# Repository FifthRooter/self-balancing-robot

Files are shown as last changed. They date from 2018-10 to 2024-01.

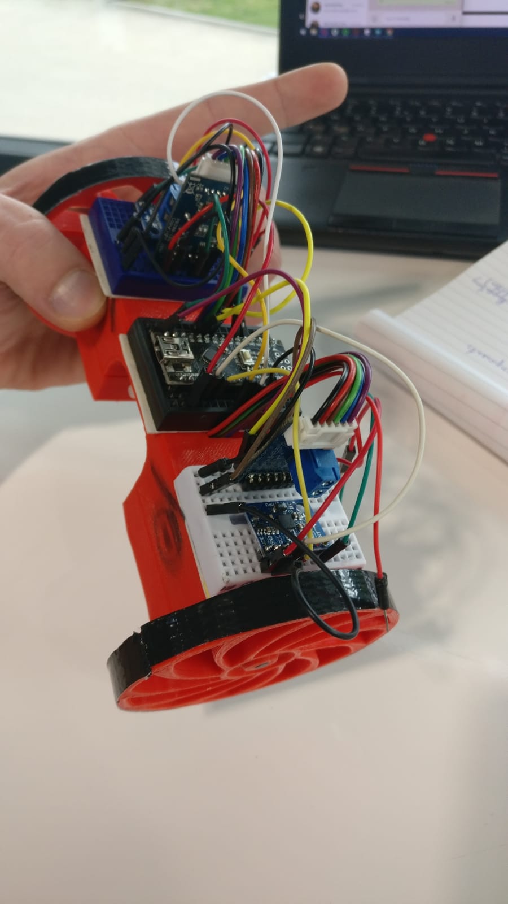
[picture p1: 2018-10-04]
graphics/v1/mark-1-angle.jpeg

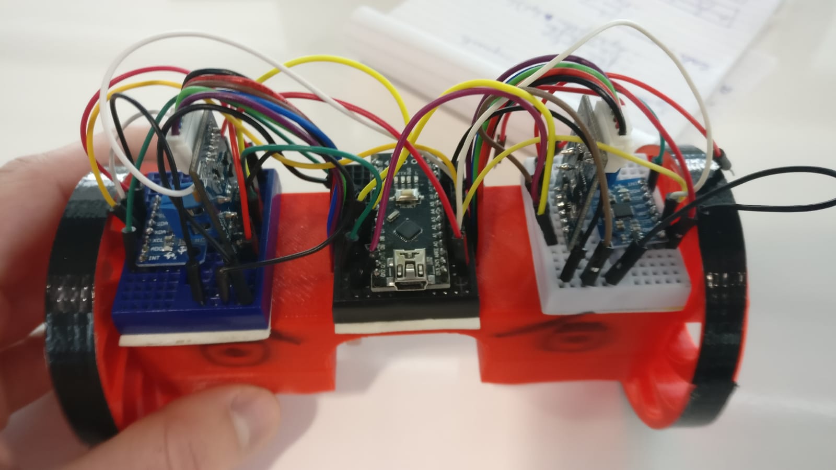
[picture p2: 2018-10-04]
graphics/v1/mark-1-top.jpeg

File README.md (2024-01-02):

### Self-balancing robot

https://github.com/FifthRooter/self-balancing-robot/assets/22204845/546c1cc7-7c90-414c-b639-572d04be5377

#### Overview
The robot is equipped with two MPU-6050 sensors that contain a 3-axis MEMS accelerometer and a 3-axis MEMS gyroscope.
The two sensors are placed at each end of the robot (above the wheels) for greater accuracy.

The design files (STLs and Solidworks) can be found in the repo under /design.

Both the accelerometer and the gyroscope individually are not sufficient to provide quality data that can be used to correct the robot’s tilt and always keep it aligned. 

That’s because the gyroscope only measures angular velocity which means that there is no fixed reference point apart from the initial calibration that can be done at the beginning of the robot test by aligning it properly and using the velocity measurements to calculate angular displacement and correct the robot accordingly. 

This requires integrating the velocity data, which would quickly become useless as integration would increase the error with time, rendering the original reference point moot. Every angular displacement calculation would contain an error, which would keep adding up with every integration step, leading to an increasingly larger errors, making the system unstable.

The accelerometer, however, can be used without the gyroscope, as the angular displacement and velocity can be calculated by performing a double and single integration, respectively. The issue is that it cannot measure precise enough acceleration values for the project’s purposes. As the accelerometer measures acceleration, it also measures the gravitational pull of Earth, which output value would be read as 1g. This 1g reference point can be used to determine orientation relative to ground.

Thus, the accelerometer and gyroscope are an ideal combination (sensor fusion) to measure the orientation and the angular velocity of the robot, allowing for accurate compensation calculations that could be used to actuate the motors in order to keep the robot stable. A complementary filter has been implemented to merge the accelerometer and gyroscope data for greater accuracy:
complementary-filter

The robot uses a proportional-integral-derivative controller (PID) to ensure that it’s always balanced with its z-axis aligned with the gravitational pull of the planet:


Electrical diagram of the whole system:
self-balancing-robot-diagram

Electrical components:
- 2x 1:53 6V DC motors
- 2x H-bridges for motor control
- Arduino Nano
- Optional: ESP8266 for wireless control
- Optional: RPi + camera for vision
- 2x MPU-6050 sensors
- Boost converter
- 2x 18650 3.7V batteries

Libraries used:
- Wire.h  - enables communication with I2C devices (small serial devices)
- I2Cdev.h - enables interfacing/reading data from a I2C device
- MPU6050.h - allows for reading data from the MPU-6050 board

Electrical components:
- 2x 1:53 6V DC motors
- 2x H-bridges for motor control
- Arduino Nano
- Optional: ESP8266 for wireless control
- Optional: RPi + camera for vision
- 2x MPU-6050 sensors
- Boost converter
- 2x 18650 3.7V batteries

Libraries used:
- Wire.h  - enables communication with I2C devices (small serial devices)
- I2Cdev.h - enables interfacing/reading data from a I2C device
- MPU6050.h - allows for reading data from the MPU-6050 board

mark-1-angle
mark-1-front
mark-1-side
mark-1-top
mark-bottom

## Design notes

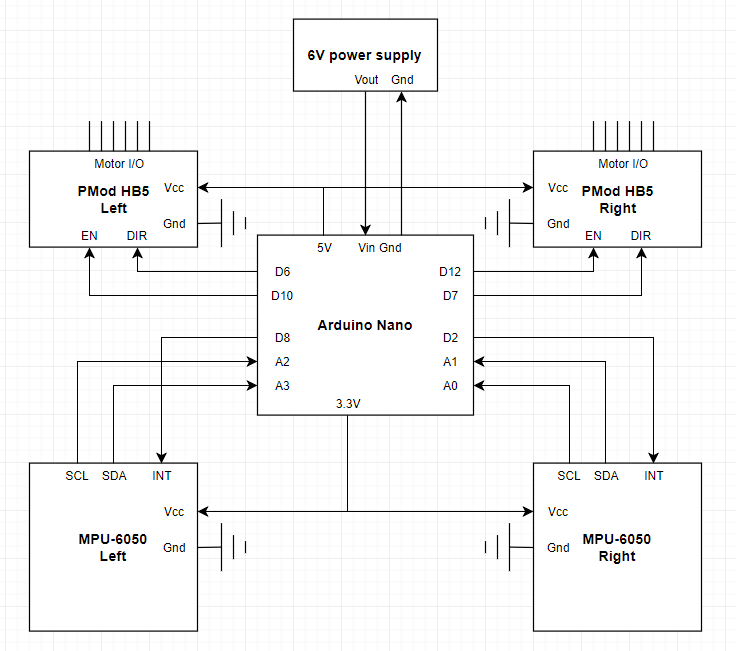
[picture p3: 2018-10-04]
graphics/diagrams/self-balancing-robot-diagram.png

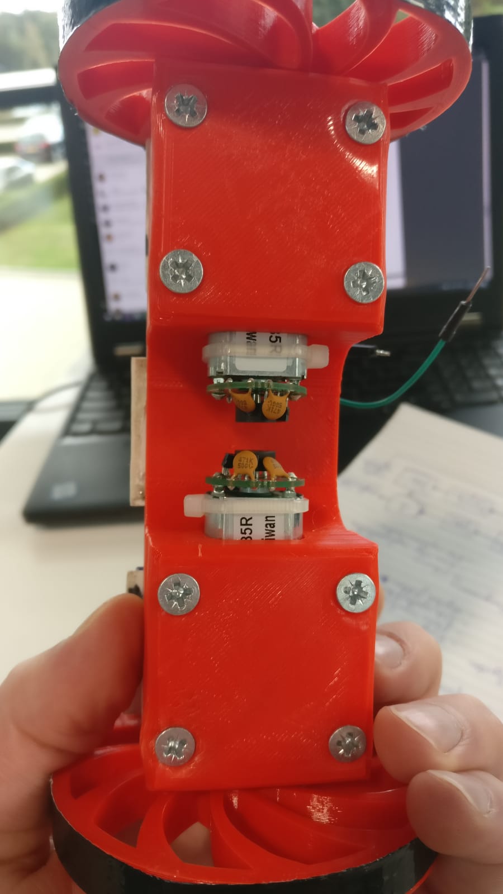
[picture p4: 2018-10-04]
graphics/v1/mark-bottom.jpeg

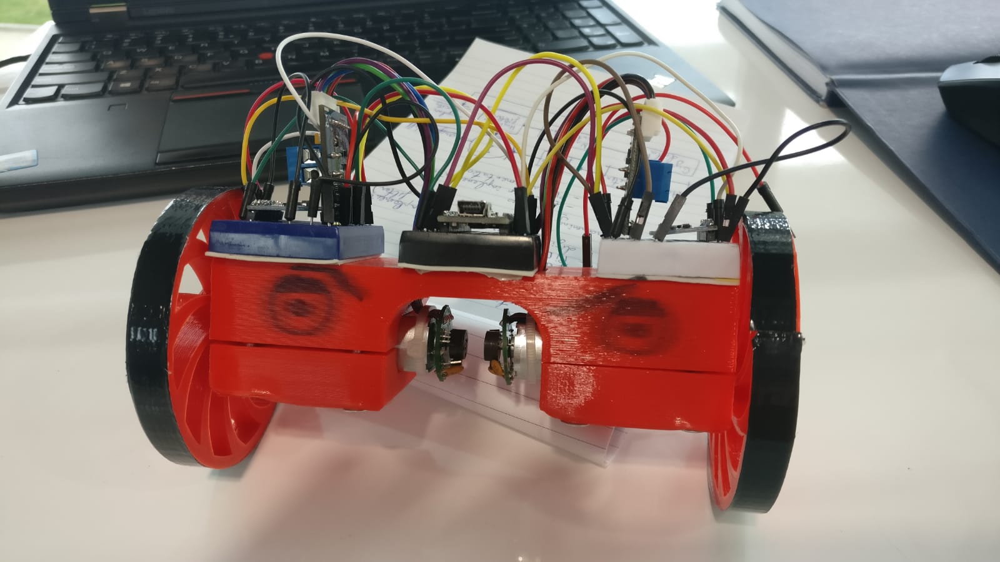
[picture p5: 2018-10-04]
graphics/v1/mark-1-front.jpeg

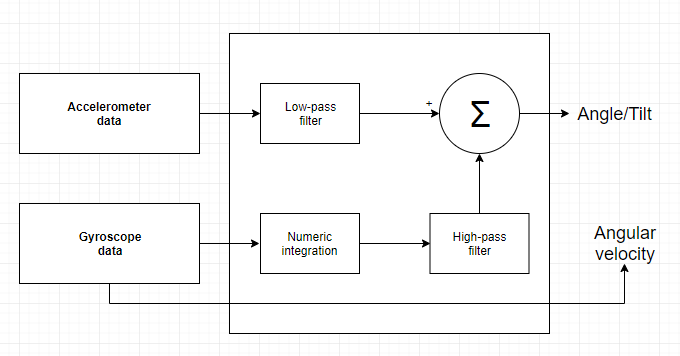
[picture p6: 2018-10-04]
graphics/diagrams/complementary-filter.png

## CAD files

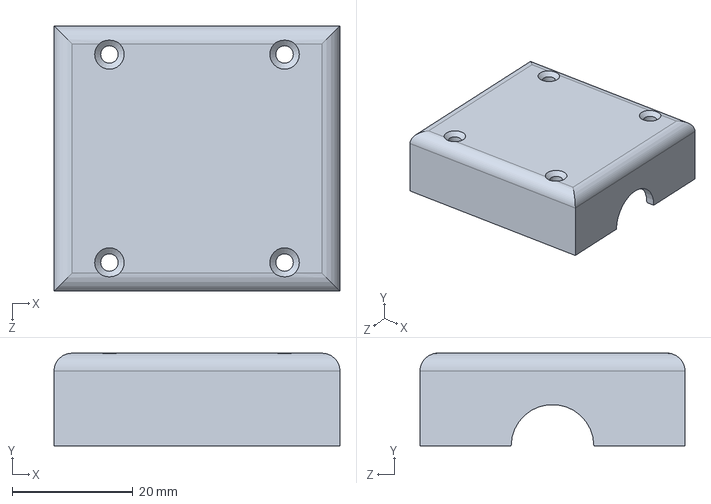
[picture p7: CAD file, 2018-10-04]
3d-design/v1/motor_sandwich.SLDPRT
47.5 x 15.4 x 44.0 mm

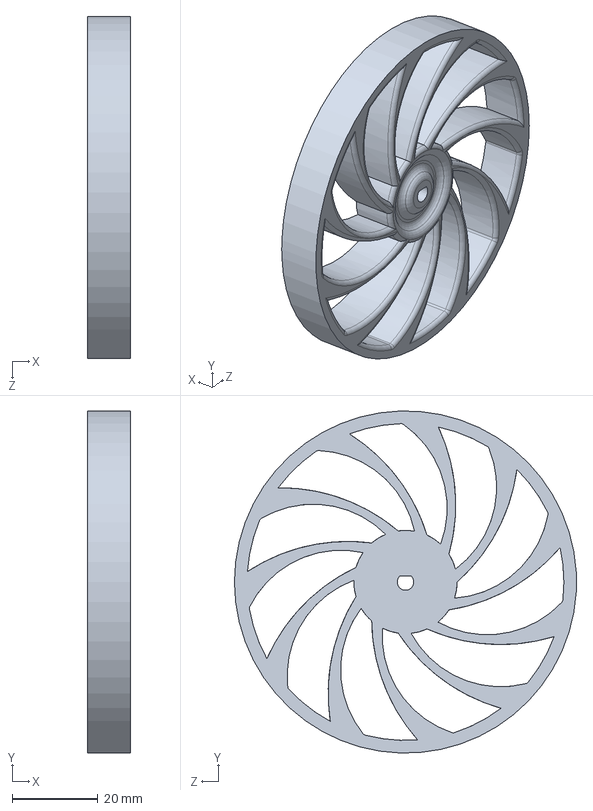
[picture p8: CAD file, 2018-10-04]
3d-design/v1/wheel.SLDPRT
10.0 x 80.0 x 80.0 mm

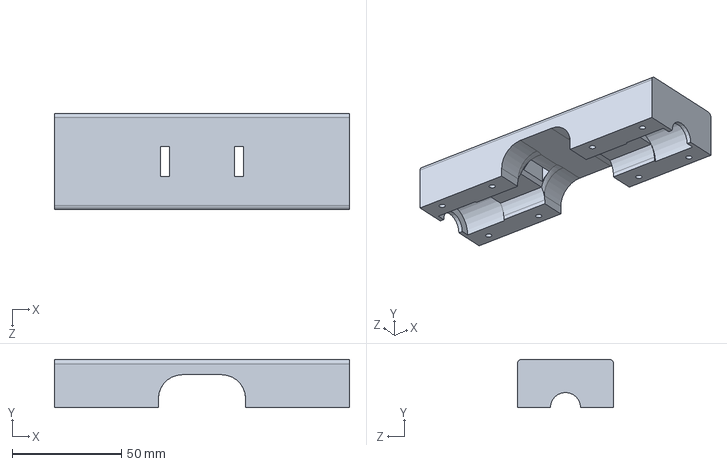
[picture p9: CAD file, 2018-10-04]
3d-design/v1/platform.SLDPRT
134.7 x 22.0 x 44.0 mm

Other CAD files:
3d-design/v1/motor_sandwich.STL
3d-design/v1/platform.STL
3d-design/v1/wheel.STL

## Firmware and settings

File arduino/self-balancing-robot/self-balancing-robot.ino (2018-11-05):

#include "Wire.h"
#include "I2Cdev.h"
#include "MPU6050.h"
#include "math.h"


MPU6050 mpu;                                    // Create an instance of the MPU6050 class

int16_t accY, accZ;                             // Define accelerometer Y and Z values as 16bit integers
float accAngle;                                 // Define the angle that will be calculated using accY and accZ values

int16_t gyroX;                                  // Define gyroscope X value (angular velocity around x-axis) as 16bit integer
float gyroAngle = 0;                            // Give the gyro angle an initial value of 0
unsigned long currTime, prevTime = 0, loopTime; // Set time-related variables as 32bit numbers of only positive value (0 to 2^32-1)

#define direction_left 5                        // Set pin number for DIR pin of left motor
#define direction_right 8                       // Set pin number for DIR pin of right motor
#define motor_pwm_left 6                        // Set pin number for EN- pin of left motor (must be a PWM pin)
#define motor_pwm_right 11                      // Set pin number for EN pin of right motor (must be a PWM pin)

#define Kp 36 // Set the proportional gain value for the PID controller
#define Ki 16.6667 //33.3333                                  //0.003 // Set the derivative gain value for the PID controller
#define Kd 0.015//0.0075
#define sampleTime 0.005                        // Define sampling time
#define targetAngle 0.5                           // Define target angle which is the desired tilt of the robot

float a = 0.0;
float tau = 0.075;
float x_angle = 0.0;

// Declare variables that are shared between the interrupt function and main loop as volatile to avoid compiler attempt to optimize the shared objects
volatile int motorPower, gyroRate;
volatile float currentAngle, prevAngle = 0, error, prevError = 0, errorSum = 0;

float complementaryFilter(float newAngle, float gyroRate, int loopTime) {
  float dtC = float(loopTime)/1000.0;
  a = tau / (tau+dtC);
  x_angle = a * (x_angle + gyroRate*dtC) + (1-a)*(newAngle);
  return x_angle;
}

void setMotors(int leftMotorSpeed, int rightMotorSpeed) {
  if (leftMotorSpeed <= 0) {
    leftMotorSpeed = leftMotorSpeed * (-1);
    leftMotorSpeed = map(leftMotorSpeed, 0, 255, 22, 255); // CCW
    analogWrite(motor_pwm_left, leftMotorSpeed);
    digitalWrite(direction_left, HIGH);
  } else {
    leftMotorSpeed = map(leftMotorSpeed, 0, 255, 22, 255); // CW
    analogWrite(motor_pwm_left, leftMotorSpeed);
    digitalWrite(direction_left, LOW);
  }

  if (rightMotorSpeed <= 0) {
    rightMotorSpeed = rightMotorSpeed * (-1);
    rightMotorSpeed = map(rightMotorSpeed, 0, 255, 0 , 255); // CW
    analogWrite(motor_pwm_right, rightMotorSpeed);
    digitalWrite(direction_right, LOW);
  } else {
    rightMotorSpeed = map(rightMotorSpeed, 0, 255, 0, 255); //CCW
    analogWrite(motor_pwm_right, rightMotorSpeed);
    digitalWrite(direction_right, HIGH);
  }
}


void initPID() {
  // initialize timer
  cli();
  TCCR1A = 0;
  TCCR1B = 0;

  OCR1A = 19999; // match register = (16000000Hz / (8*desired_frequency)) - 1 ; currently the frequency is 200HZ(5ms)
  TCCR1B |= (1 << WGM12);
  TCCR1B |= (1 << CS11);
  TIMSK1 |= (1 << OCIE1A);

  sei();
}

void setup() {
  mpu.initialize();
  Serial.begin(115200);

  pinMode(direction_left, OUTPUT);
  pinMode(direction_right, OUTPUT);
  pinMode(motor_pwm_left, OUTPUT);
  pinMode(motor_pwm_right, OUTPUT);

  mpu.setYAccelOffset(-205);
  mpu.setZAccelOffset(1398);
  mpu.setXGyroOffset(-45);

  initPID();
}

void loop() {
  // read sensor data
  accY = mpu.getAccelerationY();
  accZ = mpu.getAccelerationZ();
  gyroX = mpu.getRotationX();
  //Serial.println("accY: " + accY);
  //define the range of motor input
  motorPower = constrain(motorPower, -255, 255);
  setMotors(motorPower, motorPower);
}

ISR(TIMER1_COMPA_vect) {
  // calculate angle of inclination
  accAngle = atan2(accY, accZ) * RAD_TO_DEG;
  gyroRate = map(gyroX, -32768, 32768, -250, 250);
  gyroAngle = (float)gyroRate * sampleTime;
  //currentAngle = 0.98 * (prevAngle + gyroAngle) + 0.02 * (accAngle);
  currentAngle = complementaryFilter(accAngle, gyroRate, sampleTime*1000);
  //Serial.print(accY);
  //Serial.print(",");
  //Serial.print(accZ);
  //Serial.print(",");
  //Serial.print(gyroRate);
  //Serial.print(",");

  error = currentAngle - targetAngle;
    errorSum = errorSum + error/2*sampleTime;

  // calculate output from PID values
  
  motorPower = Kp*(error + Ki * errorSum + Kd * (error - prevError) / sampleTime);
  prevError = error;
  Serial.println(currentAngle);
  //Serial.print(",");
  //Serial.print(motorPower);
  //Serial.println("");
  prevAngle = currentAngle;
}

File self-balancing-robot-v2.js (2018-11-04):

const i2c = require('i2c-bus')
const MPU6050 = require('i2c-mpu6050')
const math = require('mathjs')
const gpio = require('pigpio').Gpio
const lcd = require('lcd')

const io = require('socket.io')()

let address = 0x68

//
// const Edgebot = mongoose.model('Edgebot', {
//   gains: {
//     Kp: Number,
//     Ki: Number,
//     Kd: Number,
//   },
//   log: {
//     timestamp: String,
//     accY: [],
//     accZ: [],
//     gyroX: [],
//     currentAngle: [],
//     elapsedTime: []
//   }
// })

// let i2c1 = i2c.openSync(1)
//
// let sensor = new MPU6050(i2c1, address)

const openSocket = require('socket.io-client')
const socket = openSocket('http://192.168.43.89:8000')

//const lcd = new Lcd({rs: 18, e: 23, data: [24, 25, 8, 7], cols: 16, rows: 2})

// socket.on('toggleMotors', () => {
//   console.log('motors toggled')
// })
let log_data_array = []

// let log_data = {
//   timestamp: '',
//   accY: [],
//   accZ: [],
//   gyroX: [],
//   currentAngle: [],
//   elapsedTime: []
// }



let accX, accY, gyroX, accAngle, gyroRate, currTime, loopTime, prevTime=0, gyroAngle=0
let motorPower, currentAngle, prevAngle=0, error, prevError=0, errorSum=0

let motorsTurnedOff = false

let Kp=80, Kd=0, Ki=0

let sampleTime = 0.025
let targetAngle = 2

const direction_left = new gpio(16, {mode: gpio.OUTPUT})
const direction_right = new gpio(12, {mode: gpio.OUTPUT})

const motor_pwm_left = new gpio(20, {mode: gpio.OUTPUT})
const motor_pwm_right = new gpio(21, {mode: gpio.OUTPUT})


let motorState = (motorsAreOn) => {
  motorsTurnedOff = motorsAreOn
}

let mapRange = (x, in_min, in_max, out_min, out_max) => {
  return (x - in_min) * (out_max - out_min) / (in_max - in_min) + out_min
}

let setMotors = (leftMotorSpeed, rightMotorSpeed) => {
  if (!motorsTurnedOff) {
    if (leftMotorSpeed <= 0) {
      leftMotorSpeed = leftMotorSpeed * (-1)
      leftMotorSpeed = mapRange(leftMotorSpeed, 0, 1200, 5, 255)
      direction_left.digitalWrite(1)
      motor_pwm_left.pwmWrite(leftMotorSpeed.toFixed())
    } else {
      leftMotorSpeed = mapRange(leftMotorSpeed, 0, 1200, 9, 255)
      direction_left.digitalWrite(0)
      motor_pwm_left.pwmWrite(leftMotorSpeed.toFixed())
    }

    if (rightMotorSpeed <= 0) {
      rightMotorSpeed = rightMotorSpeed * (-1)
      rightMotorSpeed = mapRange(rightMotorSpeed, 0, 1200, 0, 255)
      direction_right.digitalWrite(0)
      motor_pwm_right.pwmWrite(rightMotorSpeed.toFixed())
    } else {
      rightMotorSpeed = mapRange(rightMotorSpeed, 0, 1200, 0, 255)
      direction_right.digitalWrite(1)
      motor_pwm_right.pwmWrite(rightMotorSpeed.toFixed())
    }
  } else {
    motor_pwm_left.pwmWrite(0)
    motor_pwm_right.pwmWrite(0)
  }
}


// setInterval(() => {
//   let data = sensor.readSync()
//   lcd.on('ready', () => {
//     lcd.setCursor(0, 0)
//     lcd.print("Temp: " + data.temp, (err) => {
//       if (err) {
//         throw err
//       }
//     })
//   })
// }, 120)
// setInterval(() => {
  //   let data = sensor.readSync()
  //
	// 	accY = data.accel.y
	// 	accZ = data.accel.z
	// 	gyroX = data.gyro.x
	// 	accAngle = math.atan2(accY, accZ) * 180 / Math.PI
	// 	gyroRate = gyroX
  //
  //   gyroAngle = gyroRate * sampleTime
  //
  //   currentAngle = 0.99 * (prevAngle + gyroAngle) + 0.01 * accAngle
  //
  //   error = currentAngle - targetAngle
  //   errorSum = errorSum + error
  //
  //   motorPower = Kp*(error) + Ki*(errorSum)*sampleTime - Kd*(currentAngle-prevAngle)/sampleTime
  //   //motorPower = motorPower > 255 ? 255 : motorPower < -255 ? -255 : parseInt(motorPower, 10)
  //   if (motorPower > 255) motorPower = 255
  //   else if (motorPower < -255) motorPower = -255
  //
  //   setMotors(motorPower, motorPower)
  //
  //   prevAngle = currentAngle
  // }, 20)


let interval = setInterval(() => {
  let i2c1 = i2c.open(1, function (err) {
    if (err) console.log(err);

    let sensor = MPU6050(i2c1, address)

    sensor.read(function (err, data) {
      if (err) console.log(err);
      accY = data.accel.y
  		accZ = data.accel.z
  		gyroX = data.gyro.x
  		accAngle = math.atan2(accY, accZ) * 180 / Math.PI
  		gyroRate = gyroX

      gyroAngle = gyroRate * sampleTime

      currentAngle = 0.9934 * (prevAngle + gyroAngle) + 0.0066 * accAngle

      error = currentAngle - targetAngle
      errorSum = errorSum + error

      motorPower = Kp*(error) + Ki*(errorSum)*sampleTime - Kd*(currentAngle-prevAngle)/sampleTime
      //motorPower = motorPower > 255 ? 255 : motorPower < -255 ? -255 : parseInt(motorPower, 10)
      if (motorPower > 1200) motorPower = 1200
      else if (motorPower < -1200) motorPower = -1200

      setMotors(motorPower, motorPower)

      prevAngle = currentAngle
    })
  })
}, 40)


process.on('SIGINT', () => {
  //lcd.close();
  motor_pwm_left.pwmWrite(0)
  motor_pwm_right.pwmWrite(0)
  process.exit()
});


io.on('connection', (socket) => {
  console.log('connection created, robot started')
  socket.on('toggleMotors', () => {
    motorsTurnedOff = !motorsTurnedOff
  })

  socket.on('updateKp', val => {
    console.log('Kp updated: ', val)
    Kp = val
  })

  socket.on('updateKd', val => {
    console.log('Kd updated: ', val)
    Kd = val
  })

  socket.on('updateKi', val => {
    console.log('Ki updated: ', val)
    Ki = val
  })

  socket.on('moveForward', () => {
    targetAngle = 3
  })

  socket.on('moveBackward', () => {
    targetAngle = -3
  })

  socket.on('disconnect', () => {
    //clearInterval(interval)
  })

})

const port = 8000
io.listen(port)
console.log('listening on port 8000')

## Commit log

2018-10-04 added 3d models of v1
    [motor_sandwich.SLDPRT, motor_sandwich.STL, platform.SLDPRT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]
2018-10-19 update lcd test pin numbers
2018-10-19 update lcd test pin numbers v1
2018-10-22 added motor-test.js
2018-10-22 updated motor test file
2018-10-22 fix typo in main script v0
    [self-balancing-robot.js]
2018-10-22 fix typo in main script v0.1
    [self-balancing-robot.js]
2018-10-22 corrected sampleTime value to sec in main script
    [self-balancing-robot.js]
2018-10-22 convert motorPower values to ints
2018-10-22 fix typo in main script v0.2
    [self-balancing-robot.js]
2018-10-22 inverse directions for motors
2018-10-28 add socket listener functions for linear movement and PID gain control
2018-10-29 trying to fix clock issue
    [self-balancing-robot.js]
2018-11-04 update main ino file
    [robot-log.csv]
